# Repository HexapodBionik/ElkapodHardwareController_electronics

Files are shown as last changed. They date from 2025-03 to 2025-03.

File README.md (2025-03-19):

# Elkapod Hardware Controller module repository

Elkapod Hardware Controller is a module responsible for communication and control of hardware layer of Elkapod walking robot.

It abstracts components such as power supply module, servomotors, force sensors for main onboard computer - Raspberry Pi 5 - providing neat and standarized system interface.

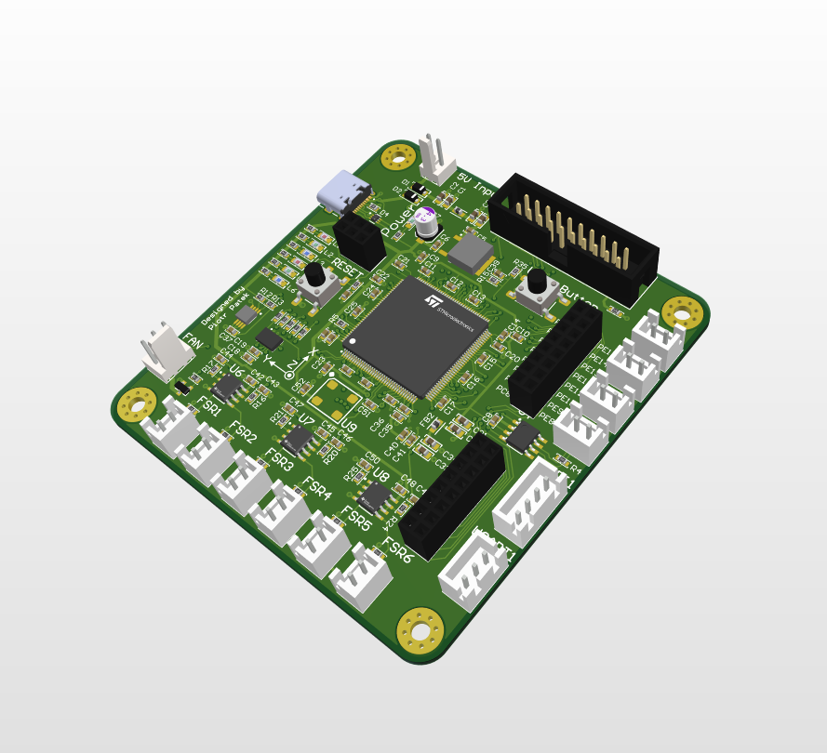
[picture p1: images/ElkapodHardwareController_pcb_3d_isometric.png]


Electronic schematics as well as mechanical drawing are available in the `docs/` folder.

## Components
Elkapod Control Module is equipped with **STM32F446ZET6** microcontroller clocked at 180MHz which lets it handle even most demanding tasks.

### User interface
User may interfact with the board using dedicated **User button**.
Along with 6 controllable LEDs with different colors it makes prototyping and debugging process easier. 
The colors are:
- L1, L2 -  <span style="color: red;">**red**</span>
- L3, L4 -  <span style="color: rgb(50, 205, 50);">**green**</span>
- L5, L6 -  <span style="color: rgb(0, 171, 240);">**blue**</span>

### Sensors
#### Inertial measurement unit (IMU)
The module has **BMI055** Bosch sensortech inertial measurement unit used for measuring current orientation of the PCB, and, thus orientation of the Elkapod's main body.

Because it is vital to have a reliable and fast response to changes in the robot's orientation, the BMI055 is connected to the MCU using an SPI bus.

#### Temperature sensor
Temperature of the environment in which the module is located is measured using MCP9808-E/MS temperature sensor connected to the MCU using I²C bus.

### Connections

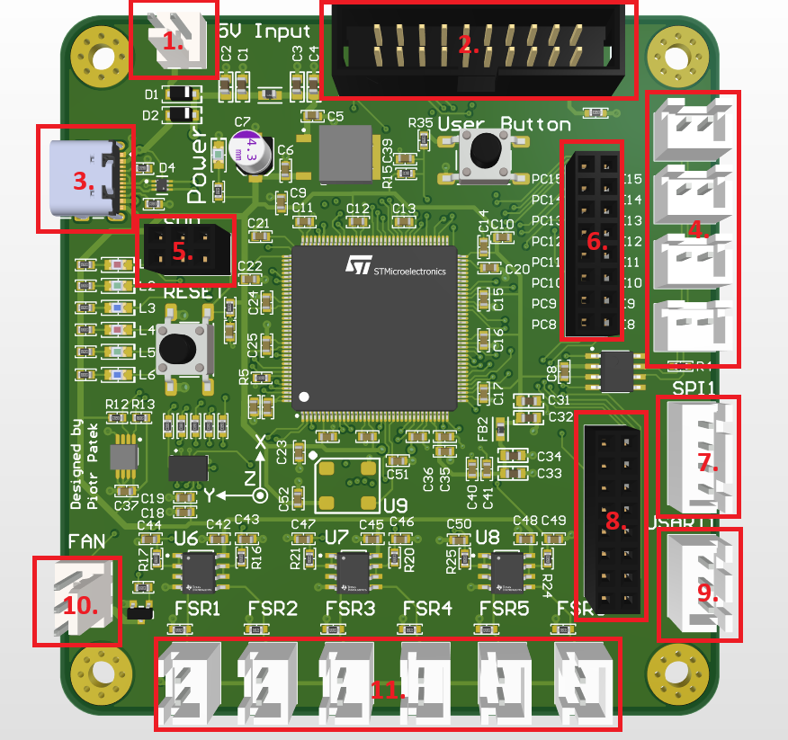
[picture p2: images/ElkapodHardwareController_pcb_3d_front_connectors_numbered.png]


The list of connections and their numbering according to the drawing above:
1. **KK power connector** - used for powering the module - power supply requirements (5V / 1.5A)
2. **IDC20 connector** - outputs PWM signals for 18 servomotors connected to the power supply board

<p align="center">
  
</p>

6. **GPIO connector 1** - generic use GPIO I/O

<p align="center">
  
</p>

8. **GPIO connector 2** - SPI bus connector used for high-speed communication with Raspberry Pi 5 

<p align="center">
  
</p>

10. **FAN connector** - KK connector for external FAN. Power parameters - 5V / up to 0.5A

<p align="center">
  
</p>

<p align="center">
  <img src="images/ElkapodHardwareController_MechanicalDrawingSide.png"">
</p>

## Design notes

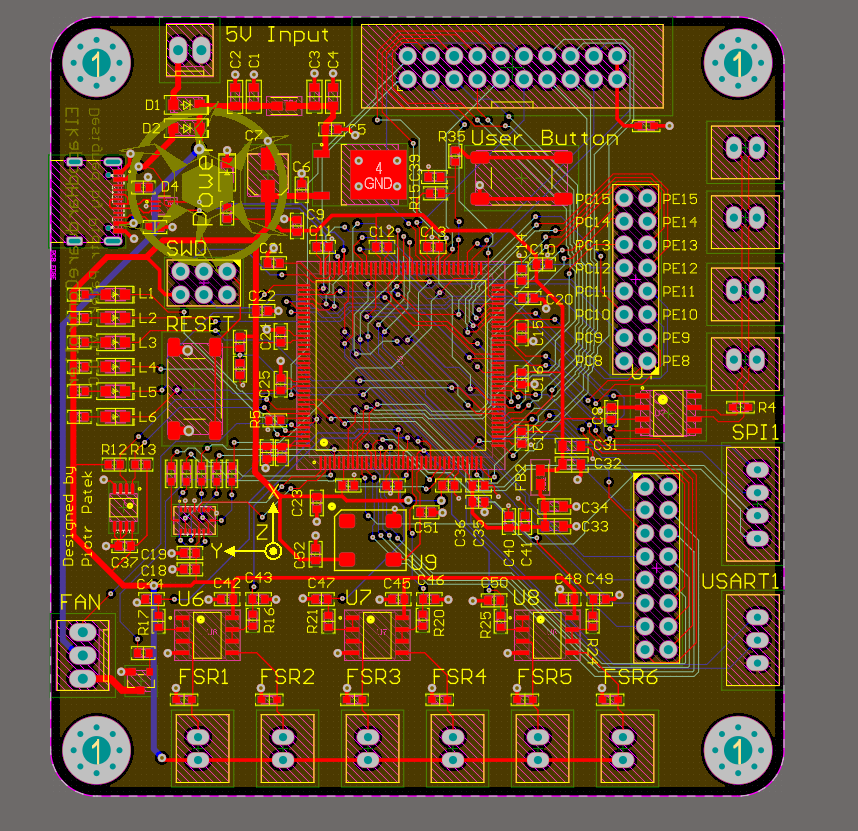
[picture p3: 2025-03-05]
images/ElkapodHardwareController_pcb_2d.png

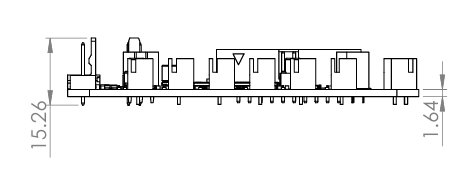
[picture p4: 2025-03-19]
images/ElkapodHardwareController_MechanicalDrawingSide.png

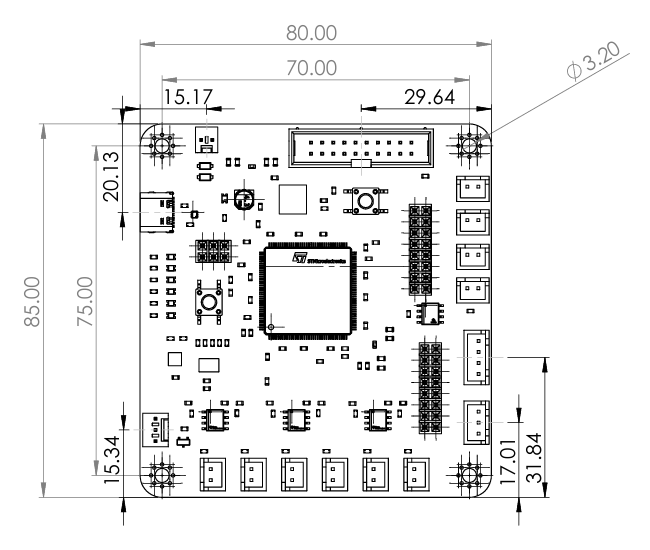
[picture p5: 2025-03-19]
images/ElkapodHardwareController_MechanicalDrawingTop.png

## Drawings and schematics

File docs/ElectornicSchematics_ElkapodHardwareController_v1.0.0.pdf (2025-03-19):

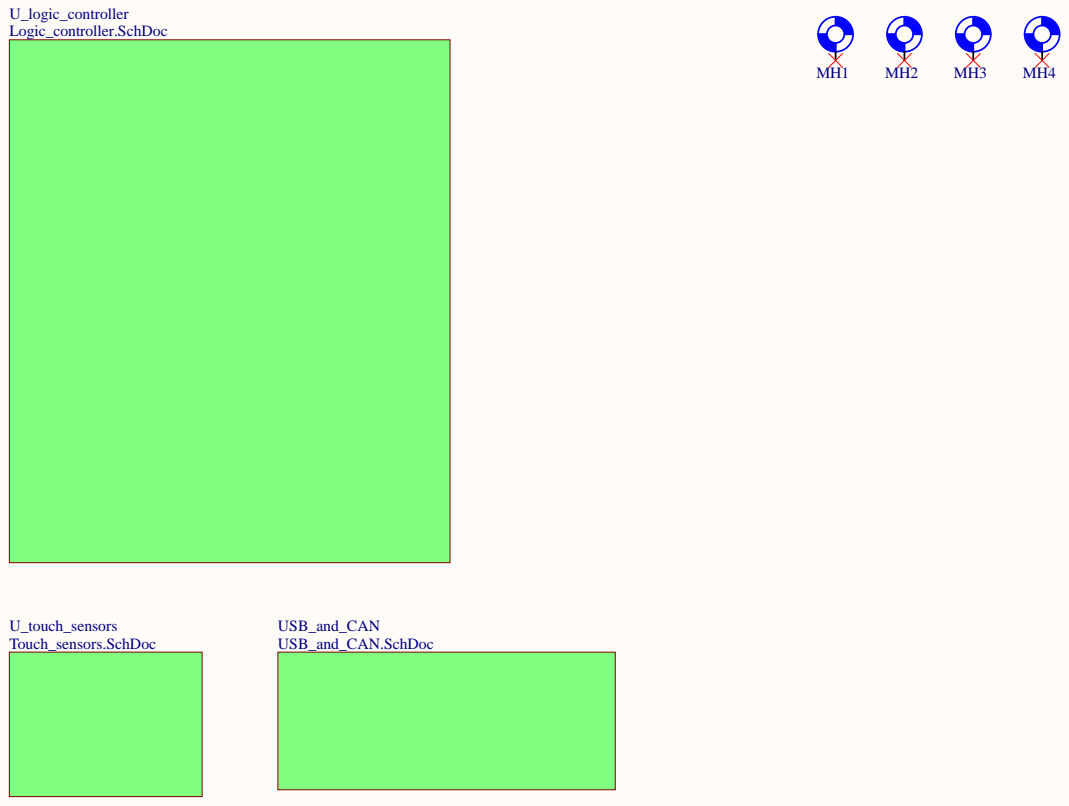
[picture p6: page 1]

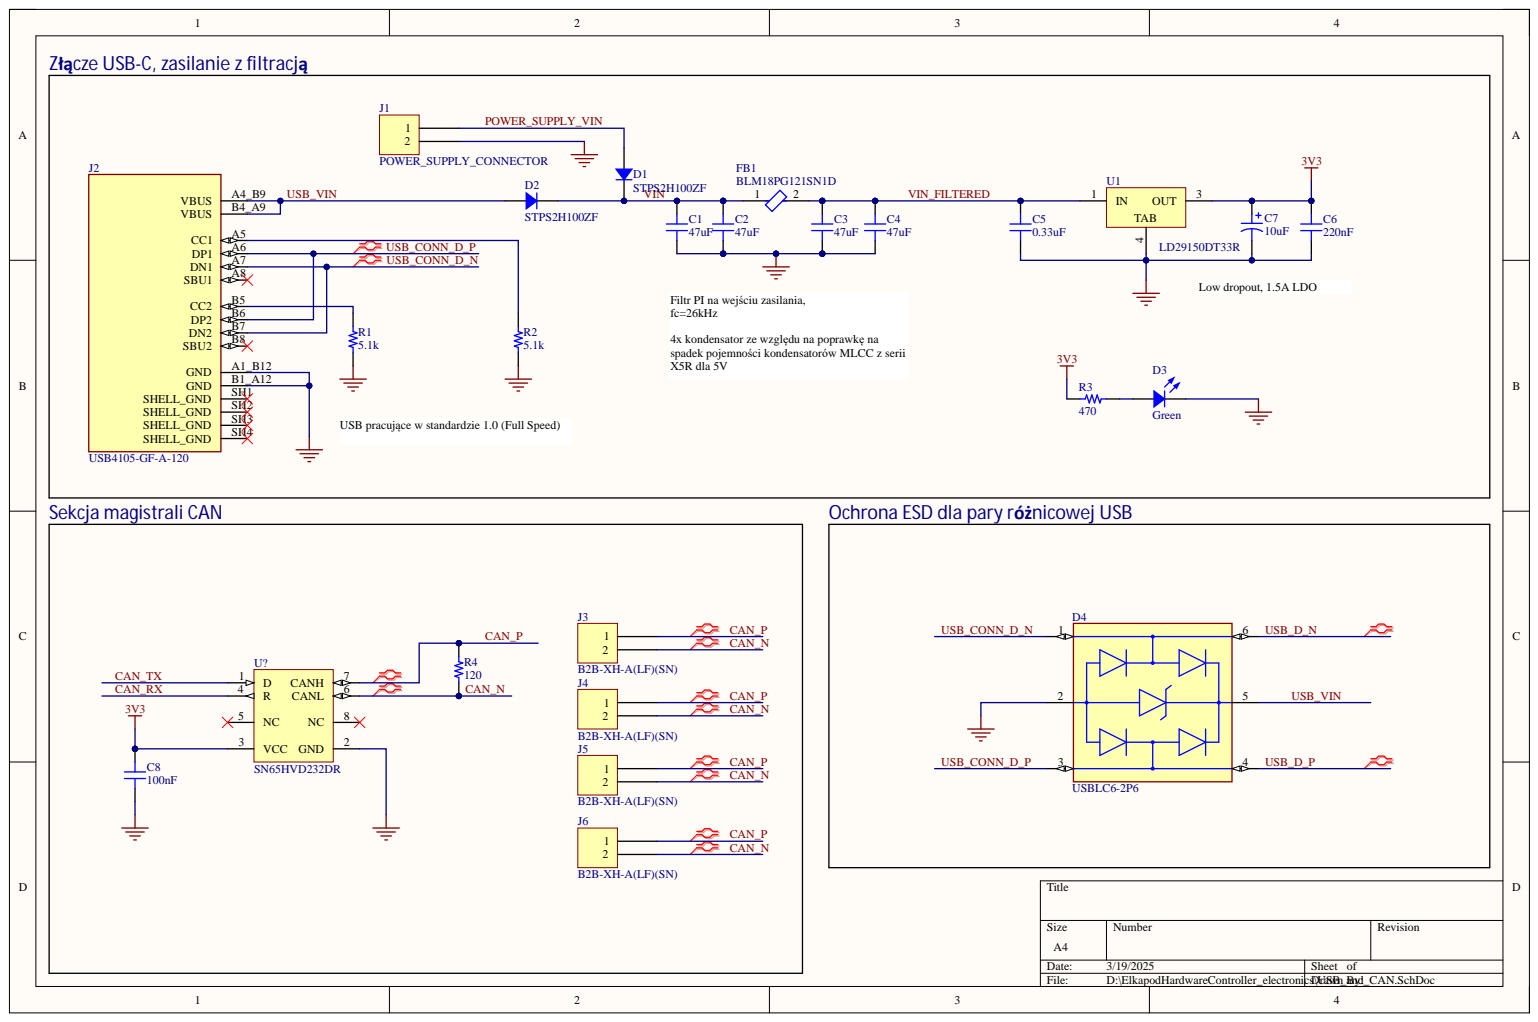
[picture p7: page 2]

Złącze USB-C, zasilanie z filtracją

Filtr PI na wejściu zasilania,
fc=26kHz

4x kondensator ze względu na poprawkę na
spadek pojemności kondensatorów MLCC z serii
X5R dla 5V

USB pracujące w standardzie 1.0 (Full Speed)

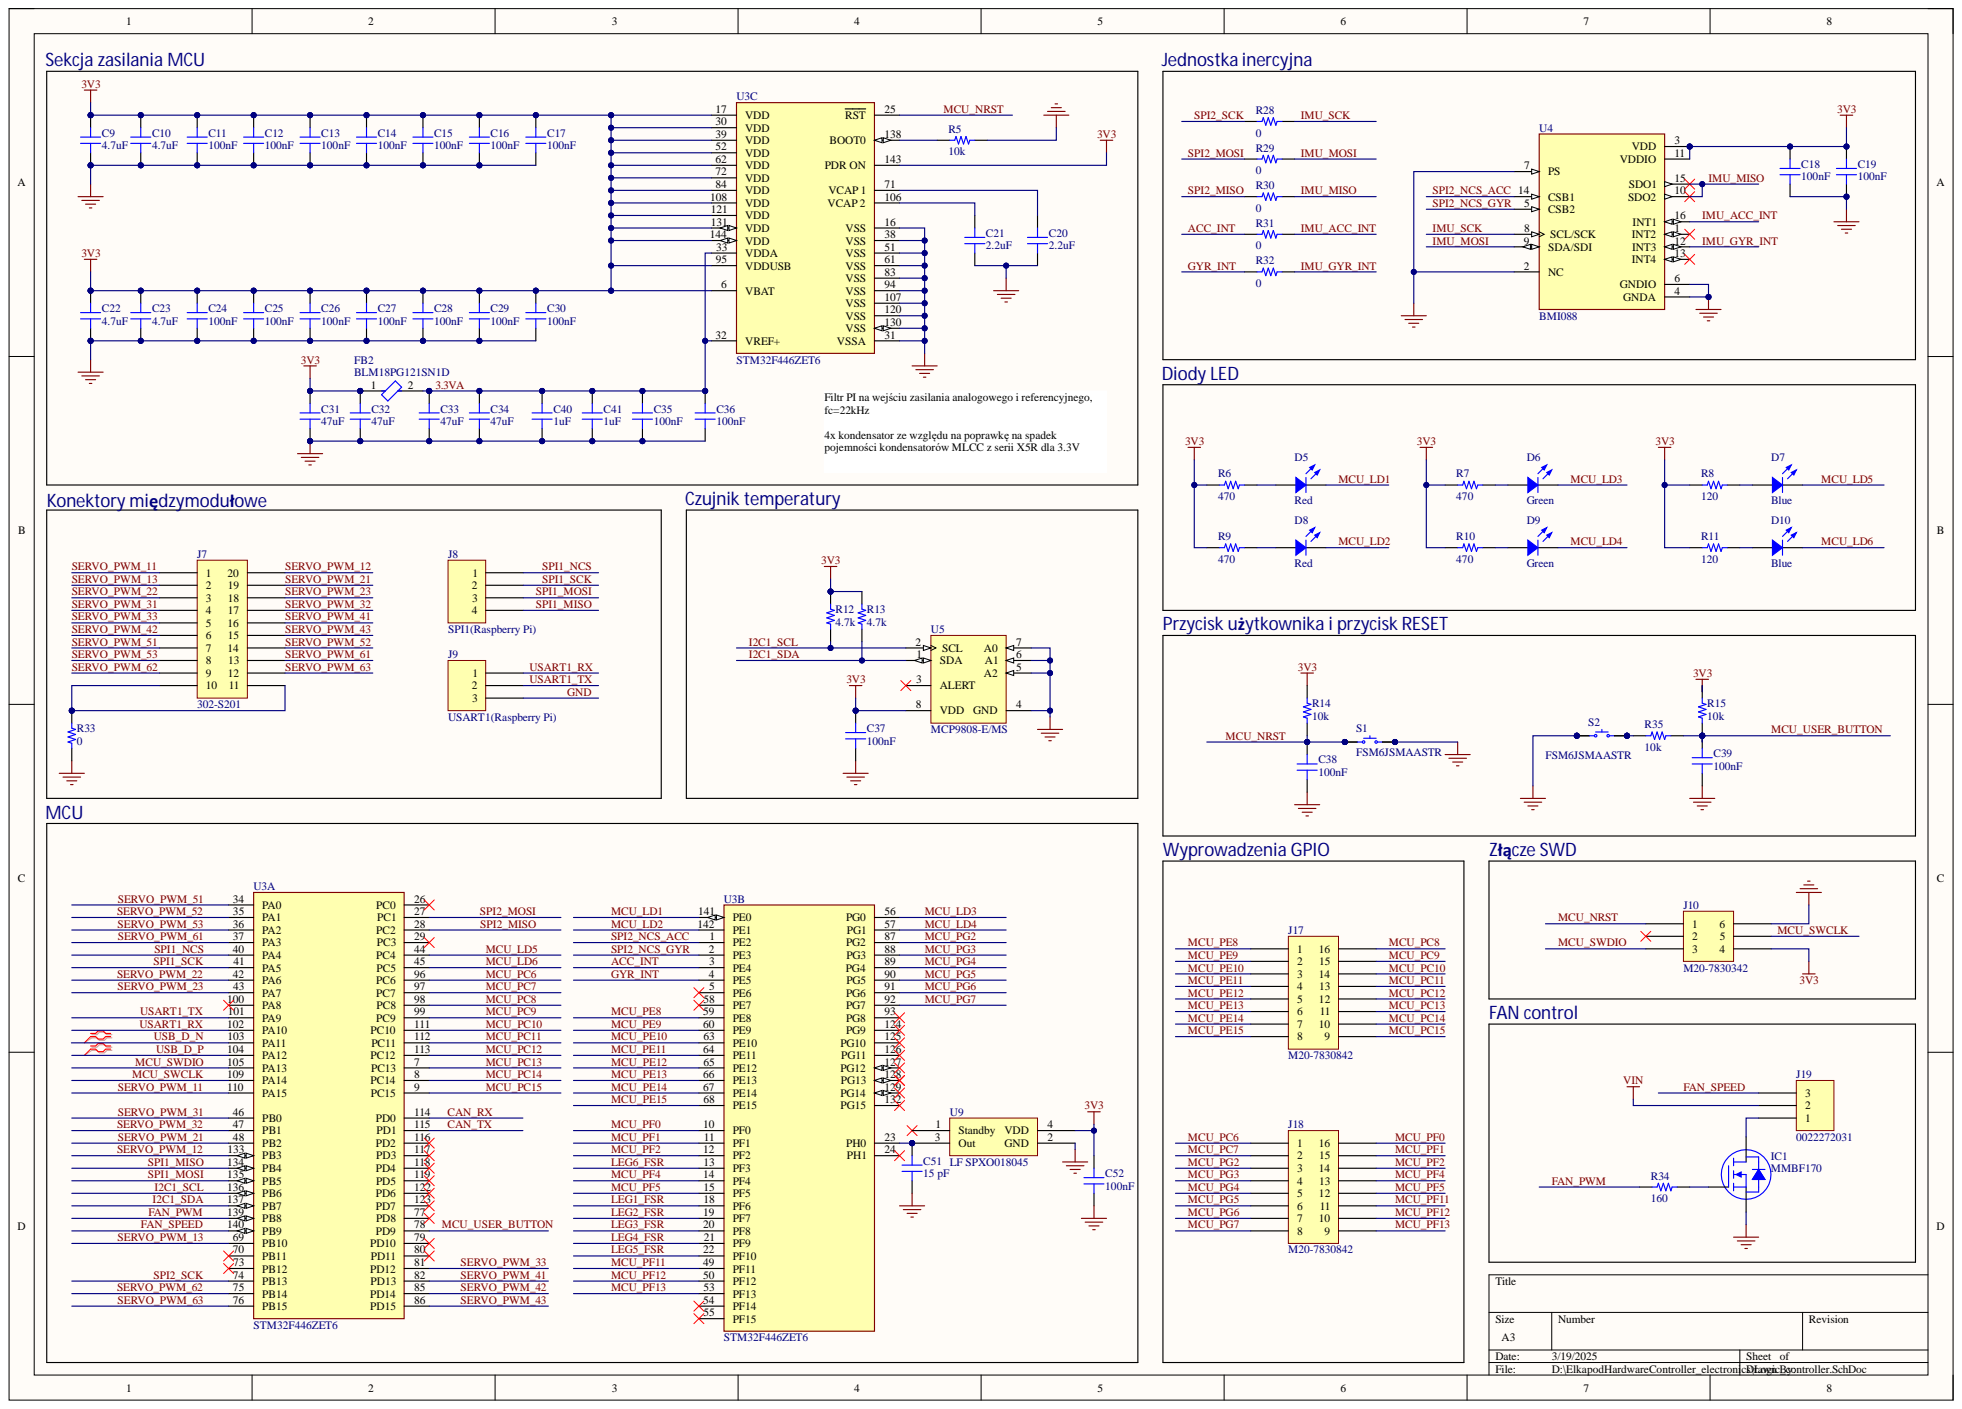
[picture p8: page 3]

Filtr PI na wejściu zasilania analogowego i referencyjnego,
fc=22kHz

4x kondensator ze względu na poprawkę na spadek
pojemności kondensatorów MLCC z serii X5R dla 3.3V

Przycisk użytkownika i przycisk RESET

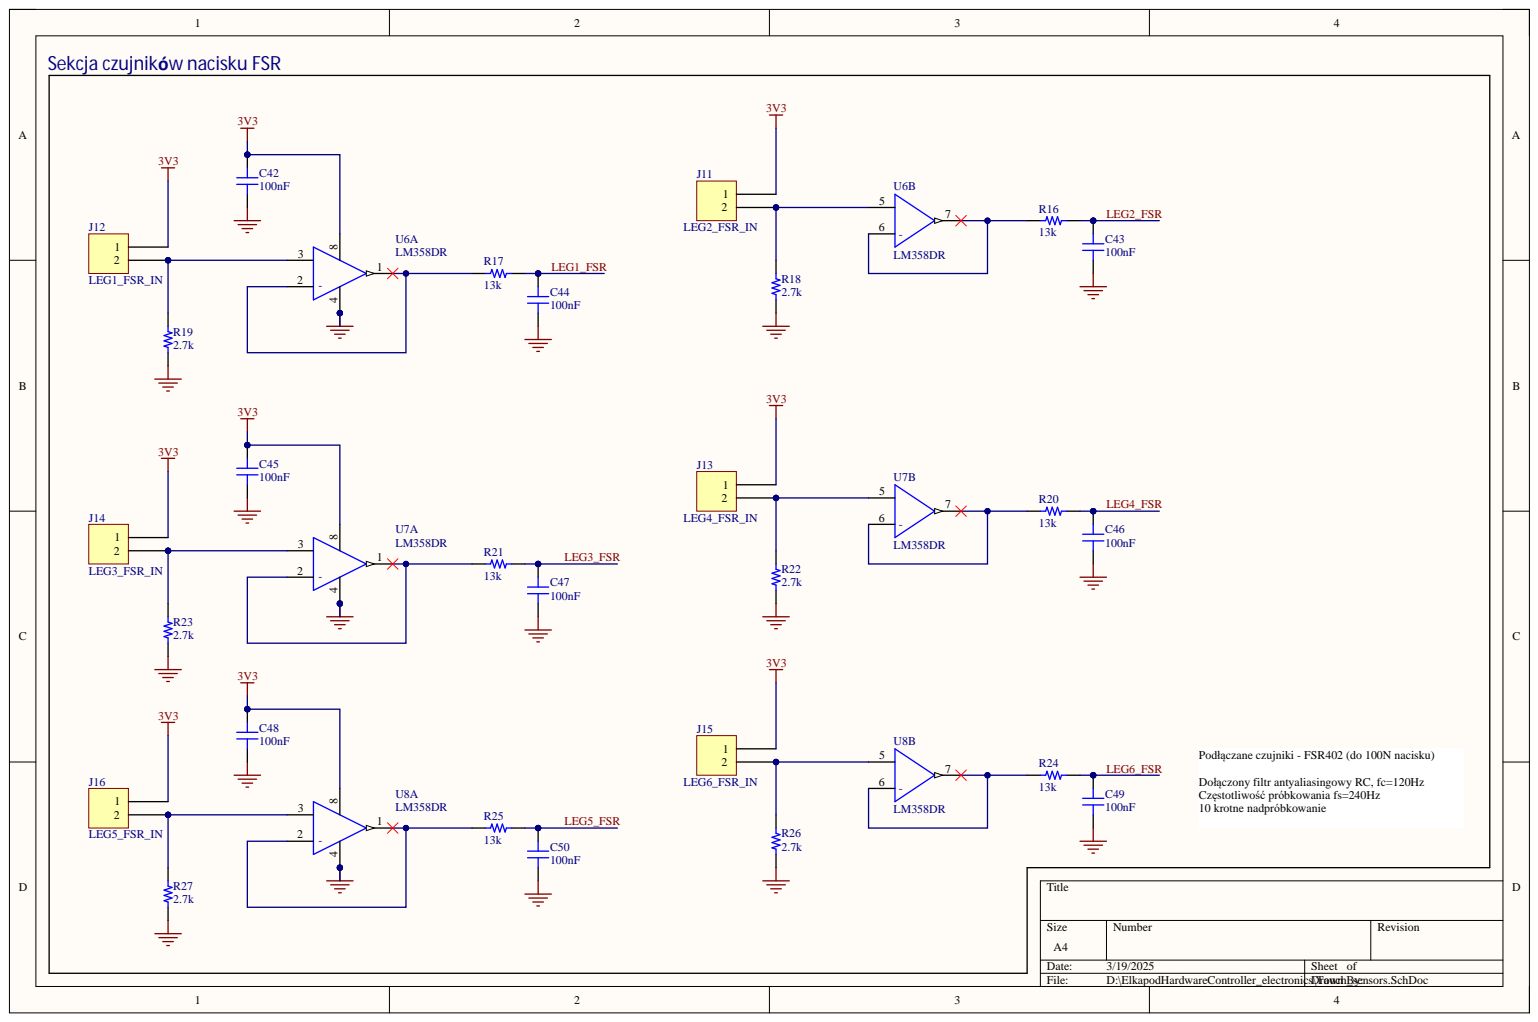
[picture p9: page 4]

Sekcja czujników nacisku FSR

Podłączane czujniki - FSR402 (do 100N nacisku)

Dołączony filtr antyaliasingowy RC, fc=120Hz
10 krotne nadpr

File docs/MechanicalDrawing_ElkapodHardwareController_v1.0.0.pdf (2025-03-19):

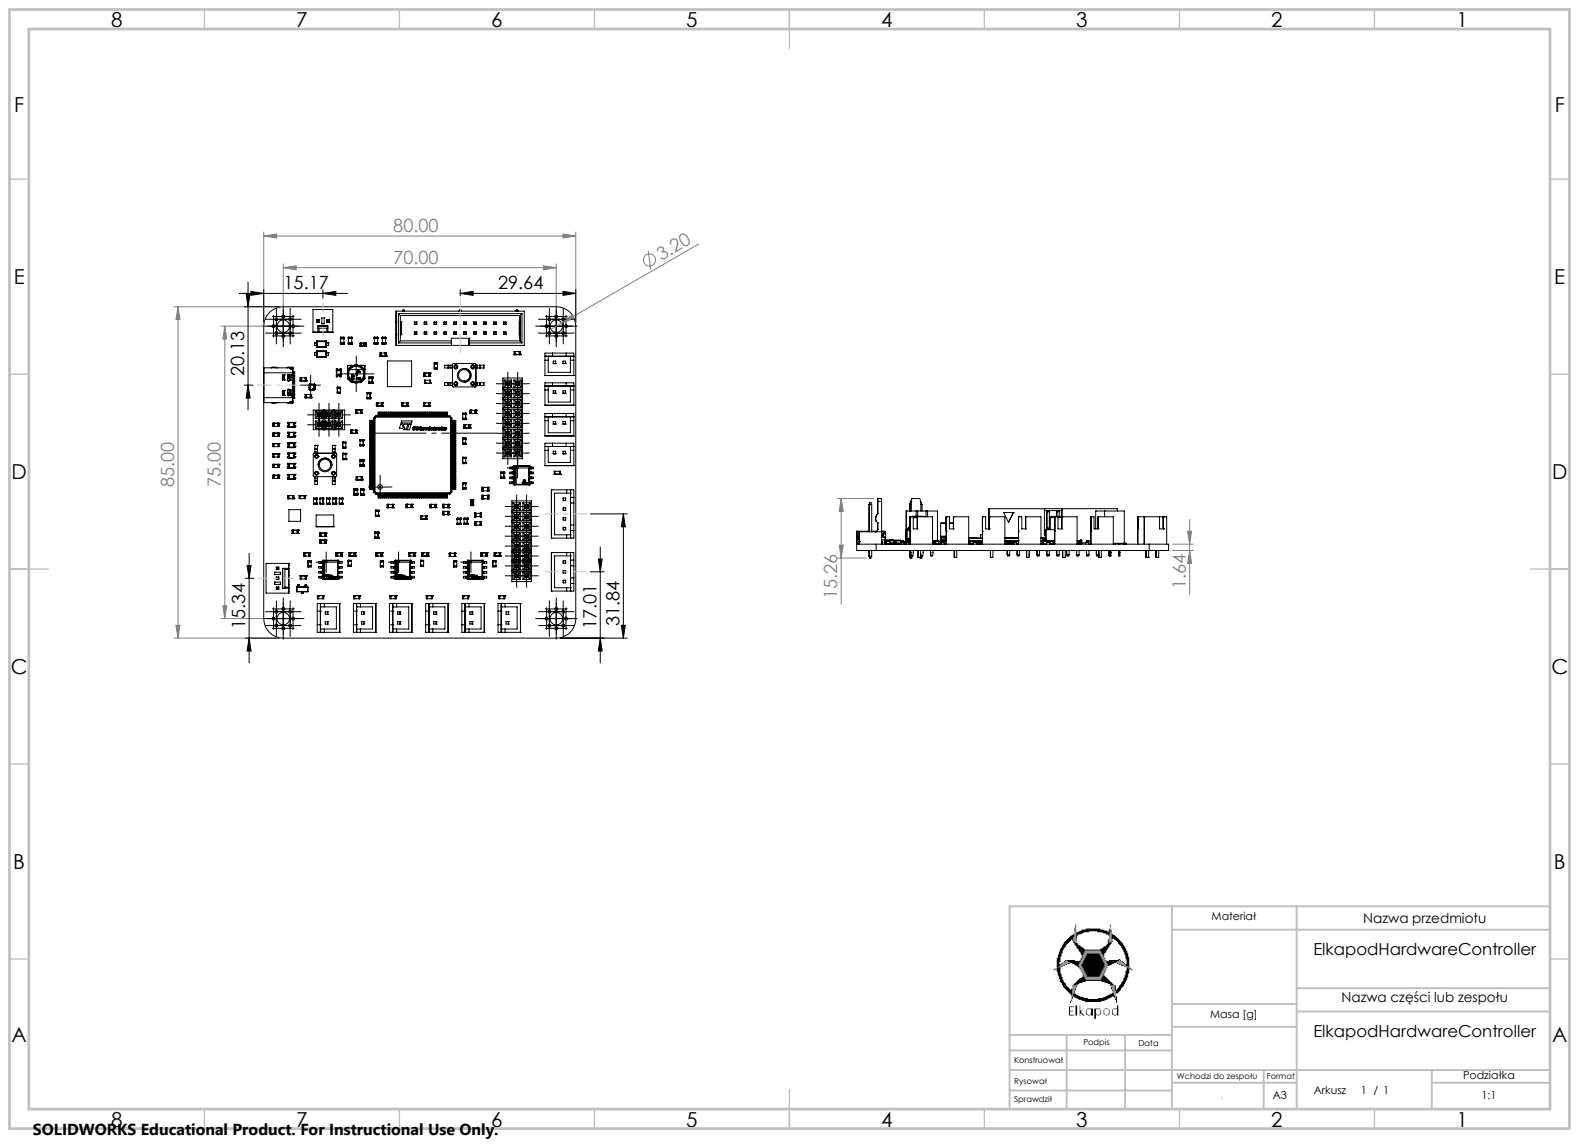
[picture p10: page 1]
Masa [g]

Materiał | Nazwa przedmiotu

ElkapodHardwareController

Nazwa części lub zespołu

Podpis | Data

Konstruował
Rysował | | | Wchodzi do zespołu | Format | Arkusz / | Podziałka

Sprawdził

SOLIDWORKS Educational Product. For Instructional Use Only.

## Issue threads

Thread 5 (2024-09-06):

figuring out the datasheet of I2C multiplexer and connecting it in proper way

kawojtowicz, 2024-09-06:

kawojtowicz, 2024-09-16:
[PCA9547-3139230.pdf](https://github.com/user-attachments/files/17011206/PCA9547-3139230.pdf)
Datasheet of I2C multiplexer

Closed 2024-09-11.

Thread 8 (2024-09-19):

connecting power supply part of stm

kawojtowicz, 2024-09-19:

kawojtowicz, 2024-09-19:
[datasheet_STM32F446ZET6.pdf](https://github.com/user-attachments/files/17059155/datasheet_STM32F446ZET6.pdf)

Closed 2024-09-20.

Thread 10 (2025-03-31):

Wrong SWD connector pinout order

VisteK528, 2025-03-31:

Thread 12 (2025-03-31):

Fix connectors placement

VisteK528, 2025-03-31:
Connectors placement should be done with "normal" positions like (X, Y) = 10, 20mm and not (X, Y) = 10.2142, 21.389 mm
This concern almost all KK connectors, JST connectors and USB connector.

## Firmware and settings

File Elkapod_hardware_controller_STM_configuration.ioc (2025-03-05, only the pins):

Mcu.UserName=STM32F446ZETx
PA0-WKUP.Signal=S_TIM5_CH1
PA1.Signal=S_TIM5_CH2
PA10.Signal=USART1_RX
PA11.Signal=USB_OTG_FS_DM
PA12.Signal=USB_OTG_FS_DP
PA13.Signal=SYS_JTMS-SWDIO
PA14.Signal=SYS_JTCK-SWCLK
PA15.Signal=S_TIM2_CH1_ETR
PA2.Signal=S_TIM5_CH3
PA3.Signal=S_TIM5_CH4
PA4.Signal=SPI1_NSS
PA5.Signal=SPI1_SCK
PA6.Signal=S_TIM3_CH1
PA7.Signal=S_TIM3_CH2
PA9.Signal=USART1_TX
PB0.Signal=S_TIM3_CH3
PB1.Signal=S_TIM3_CH4
PB10.Signal=S_TIM2_CH3
PB13.Signal=SPI2_SCK
PB14.Signal=S_TIM12_CH1
PB15.Signal=S_TIM12_CH2
PB2.Signal=S_TIM2_CH4
PB3.Signal=S_TIM2_CH2
PB4.Signal=SPI1_MISO
PB5.Signal=SPI1_MOSI
PB6.Signal=I2C1_SCL
PB7.Signal=I2C1_SDA
PB8.Signal=S_TIM10_CH1
PB9.Signal=S_TIM11_CH1
PC1.Signal=SPI2_MOSI
PC2.Signal=SPI2_MISO
PC4.GPIO_Label=LD5
PC4.Signal=GPIO_Input
PC5.GPIO_Label=LD6
PC5.Signal=GPIO_Input
PD0.Signal=CAN1_RX
PD1.Signal=CAN1_TX
PD12.Signal=S_TIM4_CH1
PD13.Signal=S_TIM4_CH2
PD14.Signal=S_TIM4_CH3
PD15.Signal=S_TIM4_CH4
PD9.GPIO_Label=USER_BTN
PD9.Signal=GPXTI9
PE0.GPIO_Label=LD1
PE0.Signal=GPIO_Input
PE1.GPIO_Label=LD2
PE1.Signal=GPIO_Input
PE2.GPIO_Label=SPI2_NCS_ACC
PE2.Signal=GPIO_Output
PE3.Signal=GPIO_Output
PE4.GPIO_Label=IMU_ACC_INT
PE4.Signal=GPXTI4
PE5.GPIO_Label=IMU_GYR_INT
PE5.Signal=GPXTI5
PF10.GPIO_Label=LEG5_FSR
PF10.Signal=ADC3_IN8
PF3.GPIO_Label=LEG6_FSR
PF3.Signal=ADC3_IN9
PF6.GPIO_Label=LEG1_FSR
PF6.Signal=ADC3_IN4
PF7.GPIO_Label=LEG2_FSR
PF7.Signal=ADC3_IN5
PF8.GPIO_Label=LEG3_FSR
PF8.Signal=ADC3_IN6
PF9.GPIO_Label=LEG4_FSR
PF9.Signal=ADC3_IN7
PG0.GPIO_Label=LD3
PG0.Signal=GPIO_Input
PG1.GPIO_Label=LD4
PG1.Signal=GPIO_Input
PH0-OSC_IN.Signal=RCC_OSC_IN
PH1-OSC_OUT.Signal=RCC_OSC_OUT

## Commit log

2024-10-14 Added project files
    [Connection_of_encoders.SchDoc, Logic_controller.SchDoc, PCB1.PcbDoc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]
2024-10-20 Working on the libraries sharing system
    [Connection_of_encoders.SchDoc, Elkapod_hardware_controller.PrjPcb, Logic_controller.SchDoc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]
2025-02-07 Working on ElkapodHardwareController schematics
    [Connection_of_encoders.SchDoc, Elkapod_hardware_controller.PrjPcb, Logic_controller.SchDoc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]
2025-02-10 Started working on PCB, cleaned the schematic
    [Elkapod_hardware_controller.PrjPcb, Logic_controller.SchDoc, PowerSupply.SchDoc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]
2025-02-12 Probably getting to end of this
    [Elkapod_hardware_controller.PrjPcb, Logic_controller.SchDoc, USB_and_CAN.SchDoc]
2025-02-13 PCB changes
    [USB_and_CAN.SchDoc]
2025-02-13 Added jumpers to IMU, widened MCU pins' footprints, removed some nets on top layer under the MCU
    [Elkapod_hardware_controller.PrjPcb, Logic_controller.SchDoc]
2025-03-05 Added PWM Fan interface, replaced current CAN controller with SN65HVD232DR CAN controller
    [Elkapod_hardware_controller.PrjPcb, Logic_controller.SchDoc, Schield_elkapod.SchDoc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]
2025-03-05 Renamed PCB file, added images, created docs file
2025-03-19 Added electonic schematics, mechanical drawing and updated README.md
    [Elkapod_hardware_controller.PrjPcb]
